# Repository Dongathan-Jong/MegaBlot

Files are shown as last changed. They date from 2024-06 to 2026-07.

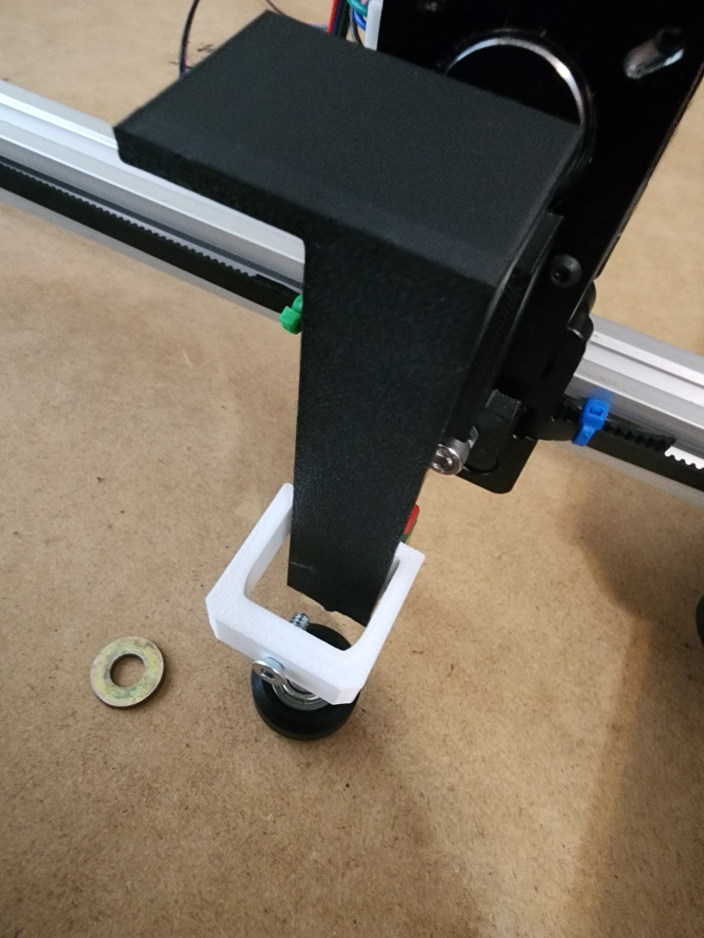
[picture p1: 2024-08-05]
how its going/20240805_174731.jpg

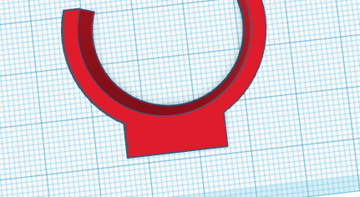
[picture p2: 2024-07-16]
how its going/image_360.png

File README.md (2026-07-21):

# MegaBlot

A pen plotter that can draw 30cm x 50cm! Controlled with an arduino and 4 stepper motors, it runs the GRBL firmware and uses the CNC shield with 4 a4988 stepper drivers.   
  
In total I spent around $200 CAD on this project, but it will cost way more if you buy it from the amazon links I provided. There are definitely cheaper alternatives online, and you can find them pretty easily through research.  

I built this as a project to pass the time while waiting for an acutal hack club blot, but it turned into an adventure of pen plotters, GRBL, and much much more.   
Check out this demo video:   
https://youtu.be/-_hqPLHjViM  

If you would like to create your own, here are the parts I used to build the project:  

# Electrical Parts  
[1x Arduino + CNC sheild + 4x a4988 Motor drivers  ](https://www.amazon.ca/DAOKI-Expansion-Arduino-Heatsink-Engraving/dp/B08KFYKKN4/  )

[4x NEMA17 Stepper Motors (I used 3x normal and 1x pancake for Z axis)  ](https://www.zyltech.com/store/stepper-motors/nema-17-motors/  )

# Mechanical Parts  
[3x 2020 aluminium extrusions](https://www.zyltech.com/2020-v-groove-extrusion-pre-cut-lengths-300mm-2000mm/?sku=EXT-2020-REG-300-VGRV) (I used 1M here but you can use any length youd like)  

[3x V-slot gantry plates + POM wheels ](https://www.amazon.ca/Standard-Aluminum-Dimensional-Printer-Accessories/dp/B0B5DY7XLH)(These are 3D printable, but they have horrible tolerances and are not rigid enough for precise drawings)  

A ton of m5 bolts, washers, nuts, and V groove nuts. (didn't really keep count of how many!)  [here](https://www.amazon.ca/Screws-Stainless-Thread-Bright-Machine/dp/B09TDRJ5GR/) or [here](https://www.amazon.ca/Boeray-Carbon-Hammer-Aluminum-Extrusion/dp/B01G7ZYHHI/)

[1x 5m GT2 belt](https://www.amazon.ca/HICTOP-Printer-Timing-Meters-Creality/dp/B00YMM6IQW/) (you might need more! YMMV)  

[3x belt tensioner](https://www.amazon.ca/Garosa-Straighten-Synchronous-Stretching-Straightening/dp/B09QKPZSHZ/) (you can replace these with 3d printed parts)

[1x Linear rail](https://www.zyltech.com/zyltech-mgn9-linear-rail-with-single-or-double-carriage-block/  ) (you only need 10cm/100mm)  

[6mm x 2mm Neodymium magnets](https://www.amazon.com/MIN-CI-Refrigerator-Whiteboard-Decorative/dp/B096LYVGPS/  ) (9 magnets needed for each pen, 3 magnets needed for arm)  

and a ton of 3d printed parts!   
All 3d printed parts are printed using the bambu lab a1 mini, stock profile, 200mm/s, 30% infill.

# Printed Parts  
1. 2x y axis motor mount v2  
  

2. 2x extrusion mount v2  
  

3. 1x X axis motor mount v2  
  

4. 1x pen motor mount  
  

**Only print parts above for no pen changer, print parts under this for pen changer!**  

5. 1x Pen Holder arm  
  

6. 2020 pen mount + pen mount (print for as many pens as youd like, each pen will need both)  

  

# Electronics  
For the arduino case, you can make any one you want, I just found one off of thingiverse. 

There are many tutorials on youtube as to how to build a cnc machine with this type of setup, I have linked a few that I used.  
https://www.youtube.com/watch?v=Xlkmso01vUk&t=6s  
https://www.youtube.com/watch?v=5qAwCg7XPZw (Replace the linear rods with the extrusion and vslot gantries.)  

A few notes, a 12V source is required to power this, and gets screwed into the terminals:  


And you need to make sure that the stepper motors are microstepped. Under each stepper motor driver slot, there are 6 pins, make sure they are all shorted:  
  
Short from top to bottom like so:    
  

# Software 
When everything is built correctly, upload the GRBL firmware to the arduino, there are many tutorials on youtube, but it is fairly straight forward if you have experience with arduino.   
https://www.youtube.com/watch?v=Xlkmso01vUk&t=6s

And thats about it! Have fun with the plotter, and to send gcode to it, use a program such as G-sender or UGS, and generate gcode using vpype!  
G-sender: https://sienci.com/gsender/  
UGS: https://winder.github.io/ugs_website/  
vpype: https://github.com/abey79/vpype  

:)

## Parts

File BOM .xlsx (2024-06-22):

Part | Quantity | Unit Price | Use | Total Price | Link
2020 V-Slot Aluminum Extrusion - 1M | 3 | $15.00 | Main rails that the axis' will be on | $45.00 | https://spool3d.ca/2020-v-slot-aluminum-extrusion/
NEMA17 Stepper Motor | 4 | $11.50 | Motors to move things around | $46.00 | https://www.amazon.ca/NEMA17-Stepper-Torque-Bipolar-Printer/dp/B0B1Q4CF87/
GT2 Belt | 1 | $10 | Motors will interact with this to control gantries | $10 | https://www.amazon.ca/Upgrade-Non-Slip-Version-Printer-Printers/dp/B09H5P2TWS
V-Slot Gantry | 3 | $17.00 | Gantry plates will act as axis drivers | $68.00 | https://www.amazon.ca/Assembled-Gantry-Wheels-Aluminum-Extrusion/dp/B09VBY64ZH/
Arduino + GRBL CNC Shield | 1 | $27.50 | Will run the GRBL firmware to control steppers | $27.50 | https://www.amazon.ca/DAOKI-Expansion-Arduino-Heatsink-Engraving/dp/B08KFYKKN4/
Base Plate | 1 | $35.50 | Holds everything | $35.50 | https://www.homedepot.ca/product/alexandria-moulding-3-4-inch-x-24-inch-x-48-inch-mdf-handy-panel/1000165106
Limit switches | 3 | $1.20 | Homing sequence | $3.60 | https://www.amazon.ca/InduSKY-Switch-Momentary-Roller-Switches/dp/B08736NP44/

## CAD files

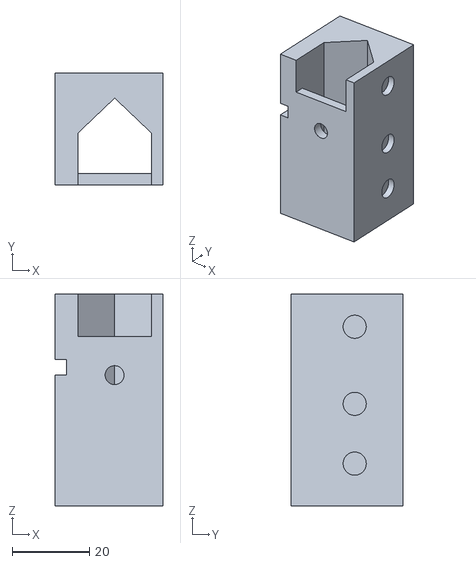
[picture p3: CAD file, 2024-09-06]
3d models/pen mount.stl
28.0 x 29.0 x 55.0

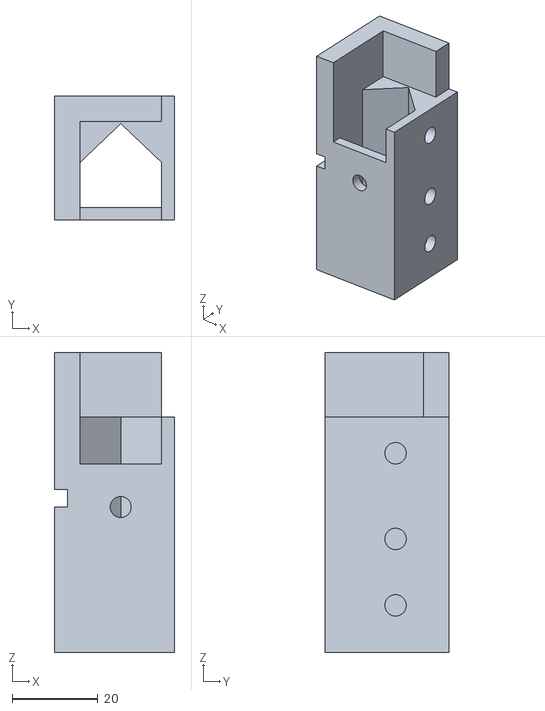
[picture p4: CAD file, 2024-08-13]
how its going/multi pen (57).stl
28.0 x 29.0 x 70.0

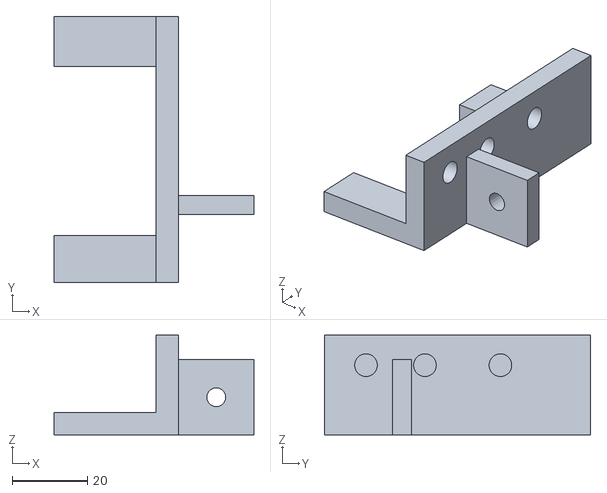
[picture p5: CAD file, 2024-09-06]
3d models/2020 pen mount.stl
53.0 x 70.5 x 26.5

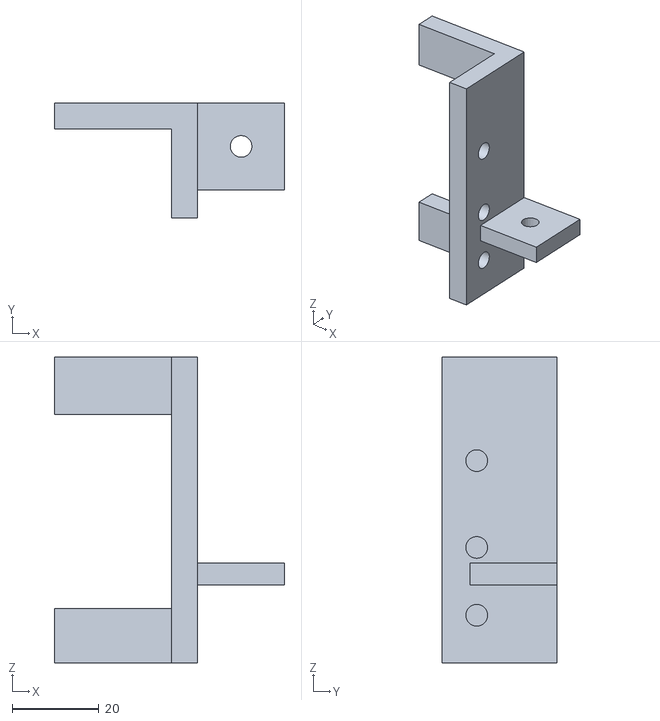
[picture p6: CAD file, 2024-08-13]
how its going/multi pen (59).stl
53.0 x 26.5 x 70.5

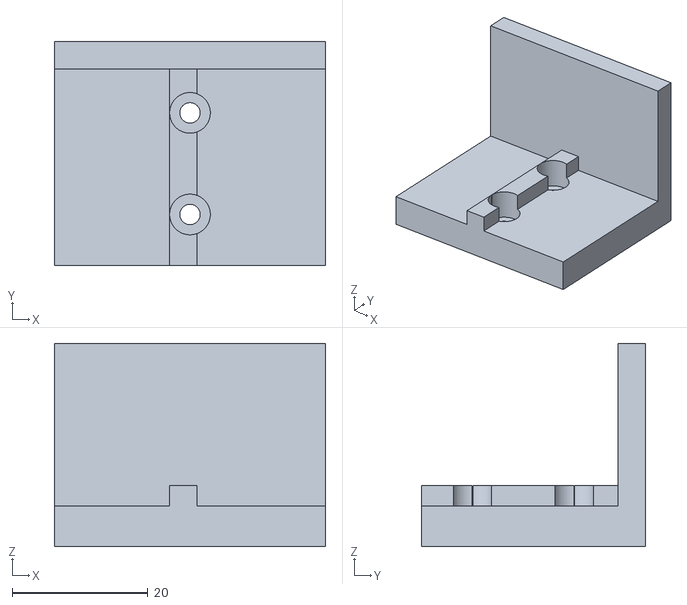
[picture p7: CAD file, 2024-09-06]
3d models/attachment arm.stl
40.0 x 33.0 x 30.0

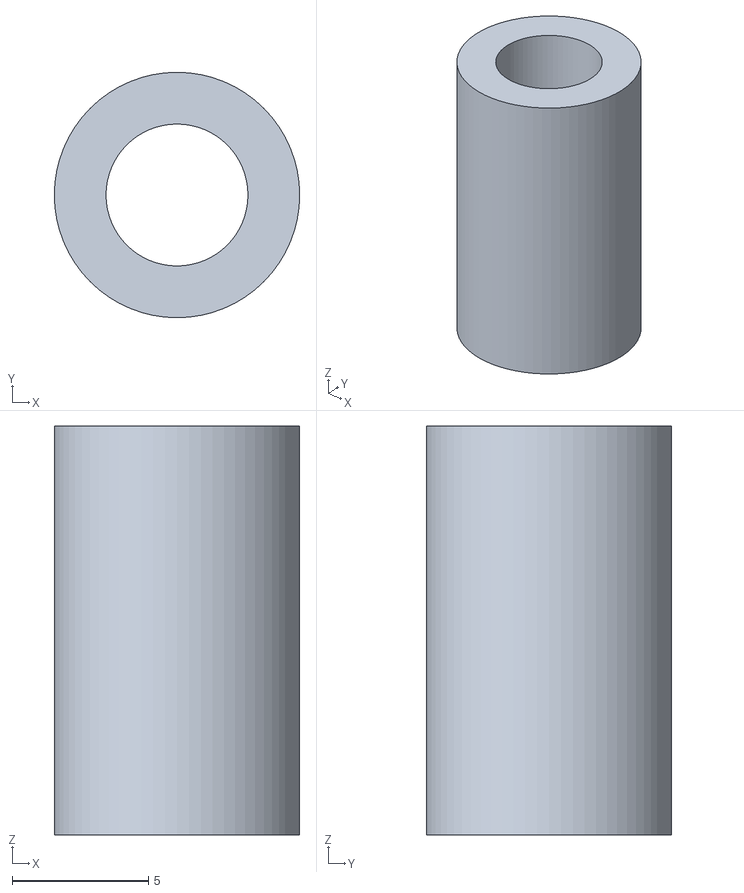
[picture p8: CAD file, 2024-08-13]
how its going/multi pen (56).stl
9.00 x 9.00 x 15.0

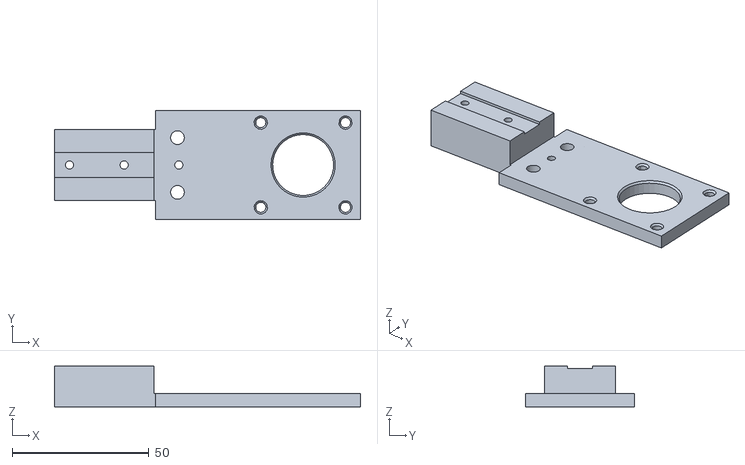
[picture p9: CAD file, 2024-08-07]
3d models/Z motor and rail mount.stl
112.0 x 40.0 x 15.0

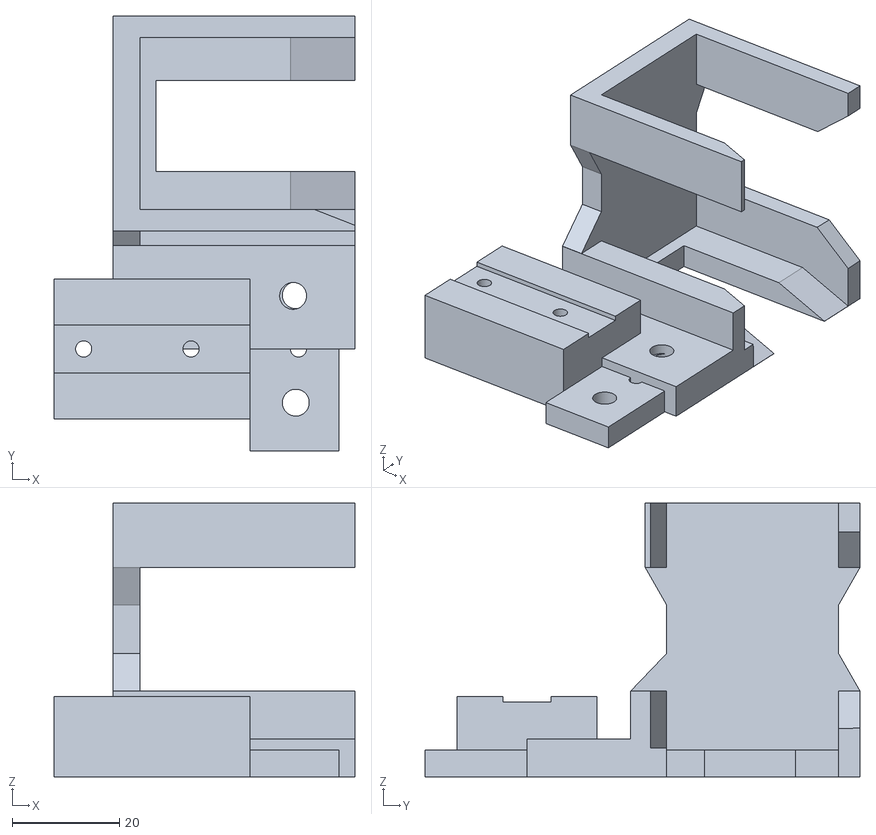
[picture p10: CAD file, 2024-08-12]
how its going/multi pen (53).stl
56.0 x 81.0 x 51.0

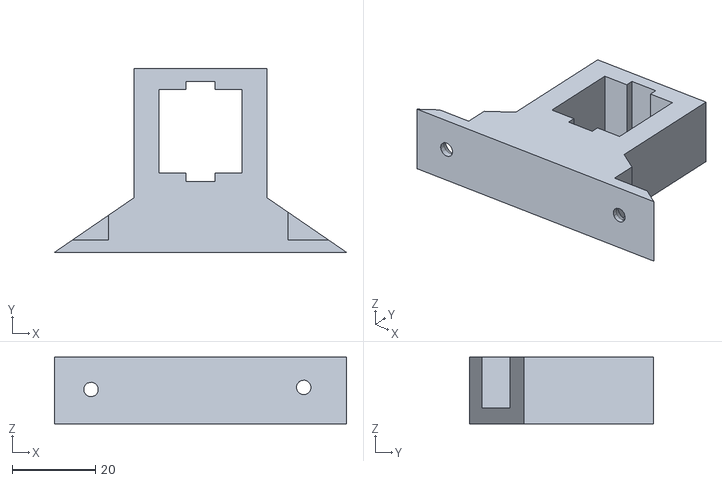
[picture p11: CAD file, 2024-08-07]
3d models/extrusion mount v2.stl
70.0 x 44.0 x 16.0

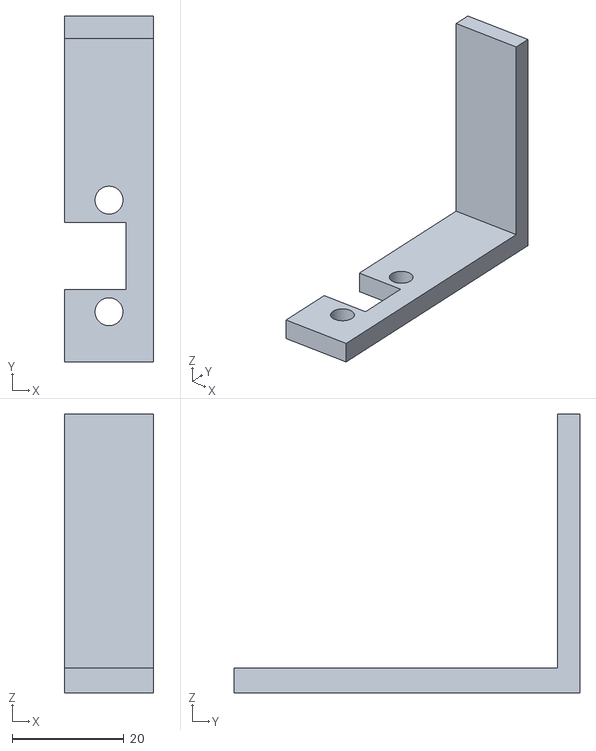
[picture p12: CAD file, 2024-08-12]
how its going/multi pen (52).stl
16.0 x 62.0 x 50.0

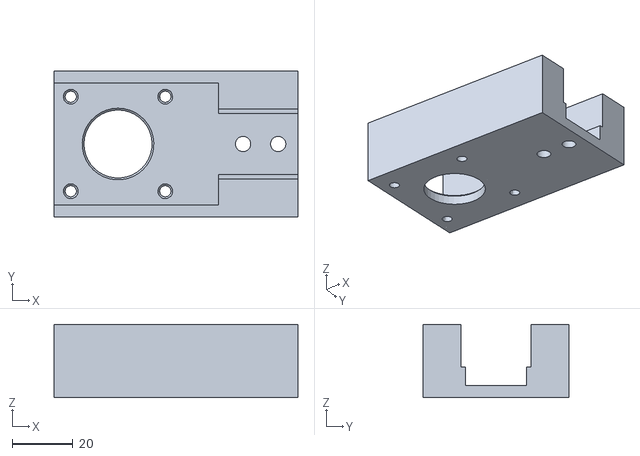
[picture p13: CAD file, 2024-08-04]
3d models/motor mount x v2.stl
80.0 x 48.0 x 24.0

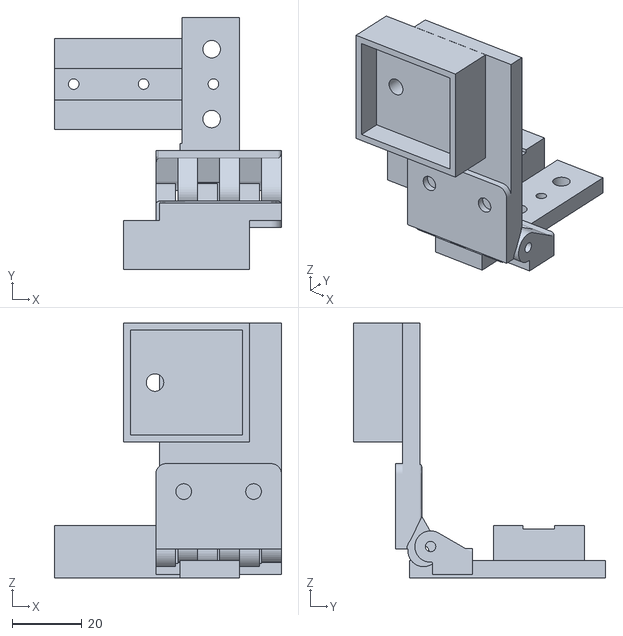
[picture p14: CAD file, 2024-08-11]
how its going/multi pen (51).stl
65.0 x 72.0 x 73.0

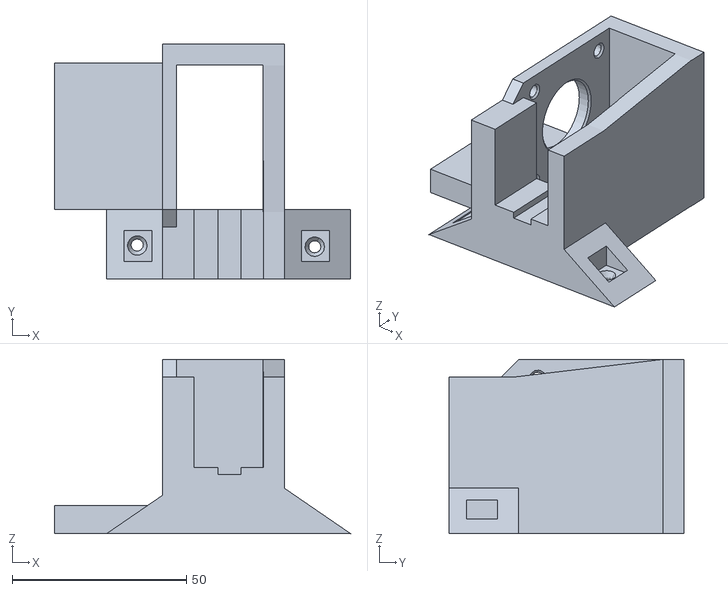
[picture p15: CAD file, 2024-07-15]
3d models/motor mount y V2.stl
85.0 x 67.5 x 50.0

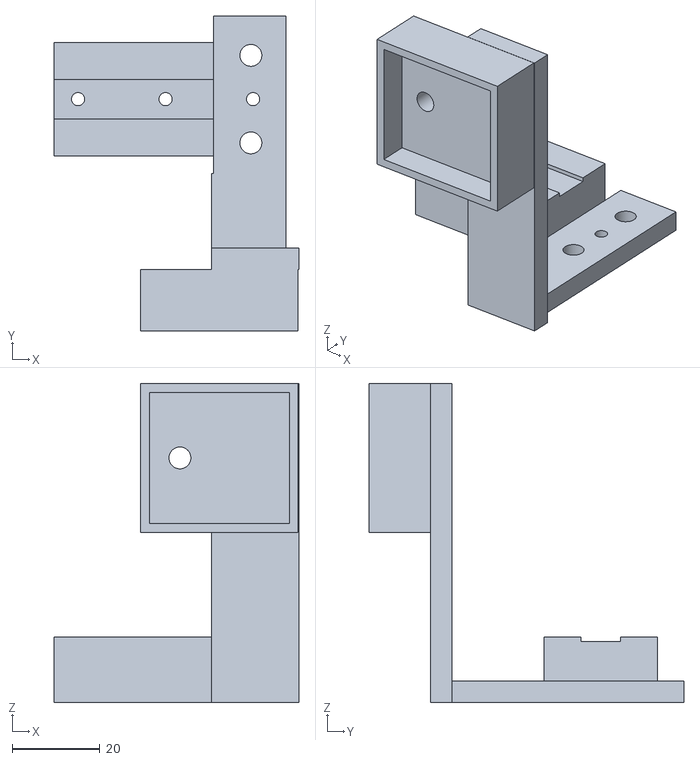
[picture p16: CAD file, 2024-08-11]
how its going/multi pen (48).stl
56.0 x 72.0 x 73.0

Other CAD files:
how its going/multi pen (44).stl
how its going/multi pen (46).stl
how its going/multi pen (45).stl
how its going/case (2).stl
3d models/extrusion mount.stl
3d models/motor mount x.stl
3d models/motor mount y.stl
how its going/2020 holder.stl
how its going/Bodacious Lappi (2).stl
how its going/cable chain.stl
how its going/extrusion mount.stl
how its going/linear rail mount.stl
how its going/motor mount.stl
how its going/multi pen (11).stl
how its going/multi pen (12).stl
how its going/multi pen (13).stl
how its going/multi pen (14).stl
how its going/multi pen (15).stl
how its going/multi pen (16).stl
how its going/multi pen (17).stl
how its going/multi pen (18).stl
how its going/multi pen (19).stl
how its going/multi pen (20).stl
how its going/multi pen (21).stl
how its going/multi pen (22).stl
how its going/multi pen (23).stl
how its going/multi pen (24).stl
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
